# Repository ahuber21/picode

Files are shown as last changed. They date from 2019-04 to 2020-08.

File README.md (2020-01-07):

# picode - All code that is run on the Saufhaengerle Raspberry Pi

* [picode - All code that is run on the Saufhaengerle Raspberry Pi](#picode---all-code-that-is-run-on-the-saufhaengerle-raspberry-pi)
  * [Links](#links)
  * [TODO](#todo)
  * [Contents](#contents)
    * [switcher](#switcher)
    * [zapfhahn](#zapfhahn)
  * [Timezone notes](#timezone-notes)
  * [Install pyfingerprint](#install-pyfingerprint)
    * [pyfingerprint - required modifications / hacks](#pyfingerprint---required-modifications--hacks)
  * [Fixing the image download from charBuffer](#fixing-the-image-download-from-charbuffer)
    * [Using fingerprint sensor](#using-fingerprint-sensor)
  * [Valve notes](#valve-notes)
  * [MariaDB notes](#mariadb-notes)
    * [phpMyAdmin](#phpmyadmin)
    * [Grafana](#grafana)

## Links

* saufanlage myPhpAdmin: http://saufanlage.local:81/http://saufanlage.local:81/phpmyadmin/
  * suffi - NU-AD-76
* saufanlage grafana: http://saufanlage.local:3000
  * admin - NU-AD-76

## TODO

* Multiple fingers per user
  * Fingerprint class?
* Only valves that are registered for user
* Auto-close when idle, i.e. no quantity for x seconds
* Logs to website
* Web terminal
* Android app with push notifications
  * some statistics for every tap
* Web interface for valve/daemon configuration
* Web interface to start calib?
* Warning when tapped quantity threshold is reached
* 4 digit display

Code here is set up for python version 3.X and all required packages are defined in `requirements.txt`.

To set up the RPi do

```bash
# first make sure you installed python3.X + some dev libs
sudo apt-get install python3 python3-dev libtiff5-dev zlib1g-dev libfreetype6-dev liblcms2-dev libwebp-dev libharfbuzz-dev libfribidi-dev tcl8.6-dev tk8.6-dev python-tk git python3-venv emacs devscripts equivs libjpeg-dev apt-get install python3-dev
```

(most of the requirements are for `Pillow` which is required by pyfingerprint)

Now set up the virtual environment

```bash
git clone --recursive https://gitlab.com/saufhaengerle/picode
cd picode
python3.7 -m venv venv
source venv/bin/activate
pip install -r requirements.txt
```

If you want to set up the repository for development, **additional steps** are required. After completing the steps above do

```bash
pre-commit install
```

## Contents

### switcher

A webapp that can switch attached relays. Usually used for switching lights.

Notes:

* Bootstrap version 2.3.2
* Bootstrap toggle from http://www.bootstraptoggle.com/

### zapfhahn

All the code that is required to run the Zapfhahn.

## Timezone notes

Make sure that you select the correct timezone!

```bash
$ sudo raspi-config
# select Europe/Berlin in option '4. Localisation options'
```

## Install pyfingerprint

```bash
# dirty hack because pip install does not actually install the package, only sets the context
mkdir venv/lib/python3.5/site-packages/pyfingerprint
cp src/zapfhahn/hardware/pyfingerprint/src/files/pyfingerprint/pyfingerprint.py venv/lib/python3.5/site-packages/pyfingerprint
```

In order to use the Raspberry Pi's serial port I had to make change that is explained [here](https://raspberrypi.stackexchange.com/questions/45570/how-do-i-make-serial-work-on-the-raspberry-pi3-pi3b-pizerow/45571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). More informatio$

Do

```bash
sudo emacs -nw /boot/config.txt
```

and add the lines

```
enable_uart=1
dtoverlay=pi3-disable-bt
```

Further /boot/cmdline.txt needs some editing to prevent the console from using the UART

```bash
sudo emacs -nw /boot/cmdline.txt
```

and remove the following entry

```
console=serial0,115200
```

It is also necessary to disable the system service that initialises the modem so it doesn't use the UART: `sudo systemctl disable hciuart`.

After rebooting, this will make the uart pins available as `/dev/ttyAMA0` or better `/dev/serial0`.

To install minicom use

```bash
$ sudo apt-get install minicom
```

Now you can test the serial port, shortcut TX and RX on the pi and run the following code

```bash
$ sudo minicom -b 57600 -o -D /dev/serial0
```

If everything is working correctly the terminal will echo every keystroke.

### pyfingerprint - required modifications / hacks

We've tried many libraries and the different notes a bit spread over multiple READMEs.
Now we are using the pyfingerprint library directly in python and the notes about the wiring are in the [FPM-pi README](https://gitlab.com/saufhaengerle/picode/blob/master/src/zapfhahn/hardware/FPM-pi/README.md)

There is a special feature about the R551 sensor that needs a slight modification in the pyfingerprint library.
It is discussed in [this thread](https://github.com/brianrho/FPM/issues/8) and the fix for python is inspired by [these lines](if (page == 0 && group_idx == 0 && fid == 0)).

The point is that when scanning the page IDs for some reason the first bit in the first pageElement is always `False`.
This makes the library think that ID#0 is free, always.
For that reason the first entry must be skipped.
Specifically, this means replacing these lines

```python
# in pyfingerprint.py - function is getTemplateIndex(self, page)
for pageElement in pageElements:
    ## Test every bit (bit = template position is used indicator) of a table page element
    for p in range(0, 7 + 1):
        positionIsUsed = (self.__bitAtPosition(pageElement, p) == 1)
        templateIndex.append(positionIsUsed)
```

with

```python
for idx, pageElement in enumerate(pageElements):
    ## Test every bit (bit = template position is used indicator) of a table page element
    for p in range(0, 7 + 1):
        if idx == 0 and p == 0: continue
        positionIsUsed = (self.__bitAtPosition(pageElement, p) == 1)
        templateIndex.append(positionIsUsed)
```

## Fixing the image download from charBuffer

In the `loadTemplate` method something goes wrong.
We have to replace

```python
        packetPayload = (
            FINGERPRINT_LOADTEMPLATE,
            charBufferNumber,
            self.__rightShift(positionNumber, 8),
            self.__rightShift(positionNumber, 0),
        )
```

with

```python
        packetPayload = (
            FINGERPRINT_LOADTEMPLATE,
            charBufferNumber,
            self.__rightShift(positionNumber, 8),
            self.__rightShift(positionNumber, 0) & 0xFF,
        )
```

i.e., we have to add the `& 0xFF` part.

### Using fingerprint sensor

We use the [WiringPi](http://wiringpi.com/download-and-install/) library to provide the external functions.

**WiringPi is pre-installed on raspian!**

This code was developed using

```bash
pi@octopi:~/saufhaengerle/picode/src/zapfhahn/hardware/FPM-C $ gpio -v
gpio version: 2.46
Copyright (c) 2012-2018 Gordon Henderson
This is free software with ABSOLUTELY NO WARRANTY.
For details type: gpio -warranty

Raspberry Pi Details:
  Type: Pi 3, Revision: 02, Memory: 1024MB, Maker: Sony
  * Device tree is enabled.
  *--> Raspberry Pi 3 Model B Rev 1.2
  * This Raspberry Pi supports user-level GPIO access.
```

In order to use the Raspberry Pi's serial port I had to make change that is explained [here](https://raspberrypi.stackexchange.com/questions/45570/how-do-i-make-serial-work-on-the-raspberry-pi3-pi3b-pizerow/45571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). More information can also be found [here](https://www.raspberrypi.org/documentation/configuration/uart.md)

Do

```bash
sudo emacs -nw /boot/config.txt
```

and add the lines

```
enable_uart=1
dtoverlay=pi3-disable-bt
```

Further /boot/cmdline.txt needs some editing to prevent the console from using the UART

```bash
sudo emacs -nw /boot/cmdline.txt
```

and remove the following entry

```
console=serial0,115200
```

It is also necessary to disable the system service that initialises the modem so it doesn't use the UART: `sudo systemctl disable hciuart`.

After rebooting, this will make the uart pins available as `/dev/ttyAMA0` or better `/dev/serial0`.

The code can be compiled using

 ```bash
 gcc -lwiringPi -o test fpm_raspi.c
 ```

 #### Wiring

The picture shows how the sensor was connected to the RPi.

Wiring to RasPi

It is installed according to the manual, with pins 1 and 7 left disconnected.
Only the UART, 3.3V and GND pins are connected.

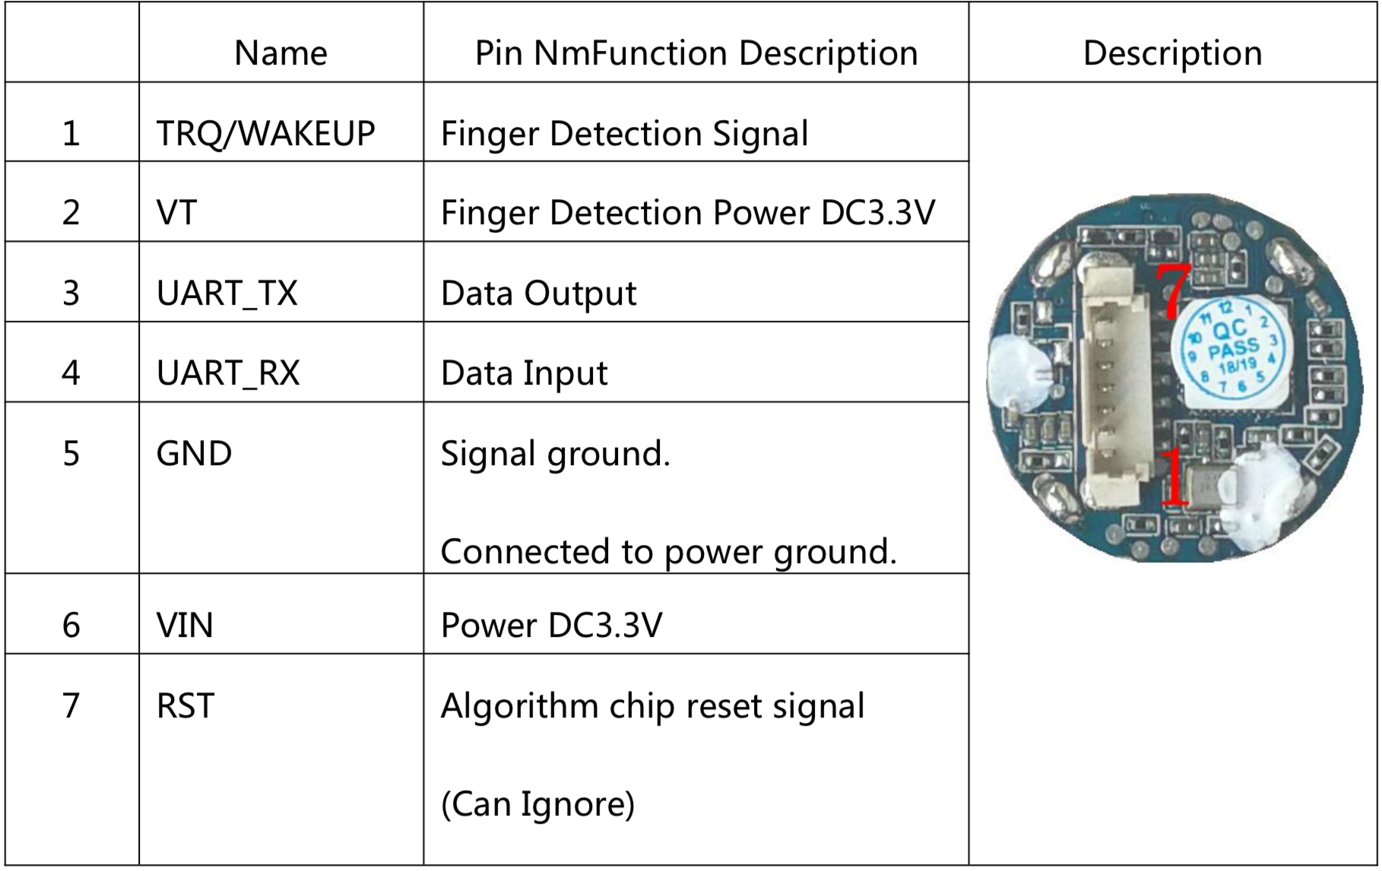
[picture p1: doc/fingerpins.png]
Fingerprint sensor pinout


The pins on the RPi 3 Model B are labeled like this

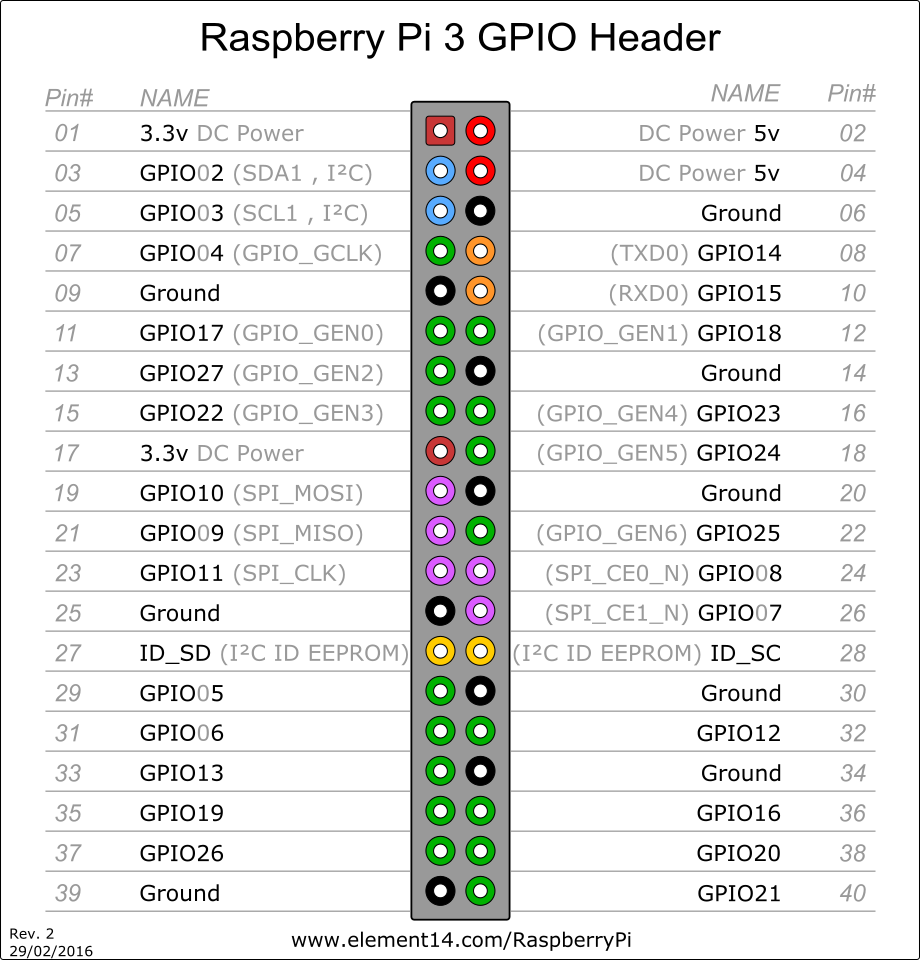
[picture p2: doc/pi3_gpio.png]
Pi Pins


The pins on the Raspberry Pi Zero are labeled like this

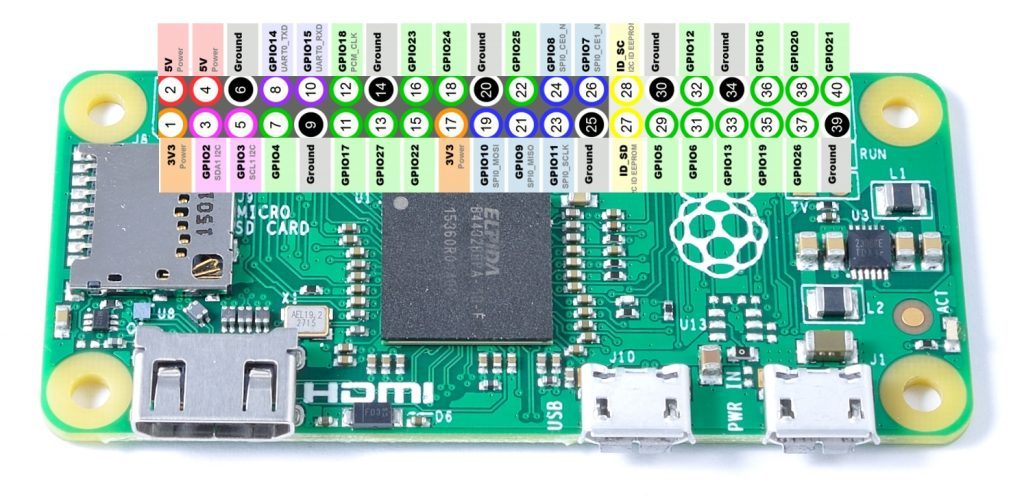
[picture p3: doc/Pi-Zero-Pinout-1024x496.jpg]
Pi Zero Pins


We have these connections

| Sensor pin | Sensor cable color | RPi pin | RPi color | Comment |
|---|---|---|---|---|
| 1 | orange | not connected | | |
| 2 | white | 3.3V/01 | black | |
| 3 | blue | GPIO15 TX/10  | orange/purple | RPi TX->Sensor RX |
| 4 | green | GPIO14 RX/08  | yellow/blue | RPi RX->Sensor TX |
| 5 | yellow | GND | green | |
| 6 | black | 3.3V/17 | yellow | |
| 7 | red | not connected | | |

## Valve notes

The valves run on 12V DC power.
The polarity does not matter.
We connect them to a relay that controls their state.
In my test setup I connected them to the normally open (NO) port.
That is because the data pin is usually in HIGH mode and we have to explicitly pull it down.
Like this, the current draw is 0 until we open it with `valve.open()`.
The logic side of the 5V relay was connected GND, Vcc = 5V and the data pin was connected to the raspberry pi **using a logic level converter**.

## MariaDB notes

```bash
sudo apt-get install mariadb-server
```

Then run the setup script

```bash
$ sudo mysql_secure_installation

NOTE: RUNNING ALL PARTS OF THIS SCRIPT IS RECOMMENDED FOR ALL MariaDB
      SERVERS IN PRODUCTION USE!  PLEASE READ EACH STEP CAREFULLY!

In order to log into MariaDB to secure it, we'll need the current
password for the root user.  If you've just installed MariaDB, and
you haven't set the root password yet, the password will be blank,
so you should just press enter here.

Enter current password for root (enter for none):
OK, successfully used password, moving on...

Setting the root password ensures that nobody can log into the MariaDB
root user without the proper authorisation.

You already have a root password set, so you can safely answer 'n'.

Change the root password? [Y/n] n
 ... skipping.

By default, a MariaDB installation has an anonymous user, allowing anyone
to log into MariaDB without having to have a user account created for
them.  This is intended only for testing, and to make the installation
go a bit smoother.  You should remove them before moving into a
production environment.

Remove anonymous users? [Y/n] n
 ... skipping.

Normally, root should only be allowed to connect from 'localhost'.  This
ensures that someone cannot guess at the root password from the network.

Disallow root login remotely? [Y/n] Y
 ... Success!

By default, MariaDB comes with a database named 'test' that anyone can
access.  This is also intended only for testing, and should be removed
before moving into a production environment.

Remove test database and access to it? [Y/n] Y
 - Dropping test database...
 ... Success!
 - Removing privileges on test database...
 ... Success!

Reloading the privilege tables will ensure that all changes made so far
will take effect immediately.

Reload privilege tables now? [Y/n] Y
 ... Success!

Cleaning up...

All done!  If you've completed all of the above steps, your MariaDB
installation should now be secure.

Thanks for using MariaDB!
```

Create a user with privileges that is allowed to connect from subnet

```
$ sudo mysql -u root
Welcome to the MariaDB monitor.  Commands end with ; or \g.
Your MariaDB connection id is 9
Server version: 10.1.38-MariaDB-0+deb9u1 Raspbian 9.0

Copyright (c) 2000, 2018, Oracle, MariaDB Corporation Ab and others.

Type 'help;' or '\h' for help. Type '\c' to clear the current input statement.

MariaDB [(none)]> GRANT ALL PRIVILEGES ON *.* TO 'suffi'@'localhost' IDENTIFIED BY 'NU-AD-76';
Query OK, 0 rows affected (0.00 sec)
```

We also add a read-only user for grafana

```bash
GRANT SELECT,SHOW VIEW ON *.* TO 'grafana'@'localhost' IDENTIFIED BY 'grafana_view_user';
```

#### Backing up the DB

Export it using

```bash
$ mysqldump -u suffi -p SaufDatabase > SaufDatabase.sql.bak
```

Import it with

```bash
# only necessary if the DB doesn't already exist
$ mysql -u suffi -p
CREATE DATABASE SaufDatabase;
```

and

```bash
mysql -u suffi -p SaufDatabase < SaufDatabase.sql.bak
```

### phpMyAdmin

```bash
sudo apt-get install phpmyadmin
# note: select apache2 if asked
# select yes when asked if you want to generate a DB
# provide password (recommended NU-AD-76)
```

Add phpmyadmin apache conf

```bash
$ sudo emacs -nw /etc/apache2/apache2.conf
# at bottom insert
Include /etc/phpmyadmin/apache.conf
# restart apache
$ sudo /etc/init.d/apache2 restart
```

If you want to make the server listen to a different port edit

```bash
$ sudo emacs -nw /etc/apache2/apache2.conf
$ sudo /etc/init.d/apache2 restart
```

Link the phpMyAdmin landing page

```bash
sudo ln -s /usr/share/phpmyadmin /var/www/html
```

Now you can connect to it, e.g. on `http://192.168.178.86:81/phpmyadmin`

### Grafana

```bash
$ wget https://dl.grafana.com/oss/release/grafana-rpi_6.2.1_armhf.deb
$ sudo dpkg -i grafana-rpi_6.2.1_armhf.deb
```

Add grafana to autostart

```bash
$ sudo /bin/systemctl daemon-reload
$ sudo /bin/systemctl enable grafana-server
```

The grafana server is listening on port 3000.
Log in on `http://192.168.178.86:3000` using user admin with password admin.
Grafana will ask you to change the PW after your first login.
Of course we change it to NU-AD-76.

There we can add a database

* Type: MySQL
* Host: localhost:3306
* Database: SaufDatabase
* User: grafana
* Password: grafana_view_user

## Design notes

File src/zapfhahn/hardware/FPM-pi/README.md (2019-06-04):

* [ahoenle:](#ahoenle)
* [Generic C library for R3xx/ZFMxx/FPMxx/R551 fingerprint modules](#generic-c-library-for-r3xxzfmxxfpmxxr551-fingerprint-modules)

## ahoenle:

Original README below, this was added by ahoenle on 2019-04-19.

_Here begins the original README:_

## Generic C library for R3xx/ZFMxx/FPMxx/R551 fingerprint modules

To use it, the following interface needs to be provided to the library, which expects function pointers with these prototypes:

    /* to get the millisecond count since reset */
    uint32_t (*fpm_millis_func)(void);

    /* millisecond delays */
    void (*fpm_delay_func)(uint32_t interval);

    /* to read from the UART port connected to the module */
    uint16_t (*fpm_uart_read_func)(uint8_t * bytes, uint16_t len);

    /* to write to the UART port connected to the module */
    void (*fpm_uart_write_func)(uint8_t * bytes, uint16_t len);

    /* to get the current number of available bytes to be read */
    uint16_t (*fpm_uart_avail_func)(void);

Check out the examples for details.

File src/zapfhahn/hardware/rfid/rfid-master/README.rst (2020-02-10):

MFRC522
=======







Arduino library for MFRC522 and other RFID RC522 based modules.

Read and write different types of Radio-Frequency IDentification (RFID) cards
on your Arduino using a RC522 based reader connected via the Serial Peripheral
Interface (SPI) interface.

.. _development:
Development
----------

**The development by owner miguelbalboa has ended**.

**Feature status: complete freeze**; no function or API change

**Code status: paritial freeze**; just fixes/typos or documentation updates; *no* extentions for other boards; *no* new examples

**Maintenance status: sporadically**

**Why no further development?**
This library has a long history and is used in many projects. This projects often do not document what version they use. Commiting changes maybe brake those old project and lead to bad experience (for beginners) and support request. For those reasons the library is in freeze mode. You can still commit typo, documentation or bug fixes.

.. _before buy:
Before buy
----------
Please notice that there are many sellers (ebay, aliexpress, ..) who sell mfrc522 boards. **The quality of these boards are extremely different.** Some are soldered with wrong/low quality capacitors or fake/defect mfrc522.

**Please consider buying several devices from different suppliers.** So the chance of getting a working device is higher.

If you got a bad board and you can tell us how to detect those boards (silk, chip description, ..), please share your knowledge.

.. _what works and not:
What works and not?
----------

* **Works**

  #. Communication (Crypto1) with MIFARE Classic (1k, 4k, Mini).
  #. Communication (Crypto1) with MIFARE Classic compatible PICCs.
  #. Firmware self check of MFRC522.
  #. Set the UID, write to sector 0, and unbrick Chinese UID changeable MIFARE cards.
  #. Manage the SPI chip select pin (aka SS, SDA)

* **Works partially**

  #. Communication with MIFARE Ultralight.
  #. Other PICCs (Ntag216).
  #. More than 2 modules, require a multiplexer `#191 <https://github.com/miguelbalboa/rfid/issues/191#issuecomment-242631153>`_.

* **Doesn't work**

  #. MIFARE DESFire, MIFARE DESFire EV1/EV2, not supported by software.
  #. Communication with 3DES or AES, not supported by software.
  #. Peer-to-peer (ISO/IEC 18092), not `supported by hardware`_.
  #. Communication with smart phone, not `supported by hardware`_.
  #. Card emulation, not `supported by hardware`_.
  #. Use of IRQ pin. But there is a proof-of-concept example.
  #. With Arduino Yun see `#111 <https://github.com/miguelbalboa/rfid/issues/111>`_, not supported by software.
  #. With Intel Galileo (Gen2) see `#310 <https://github.com/miguelbalboa/rfid/issues/310>`__, not supported by software.
  #. Power reduction modes `#269 <https://github.com/miguelbalboa/rfid/issues/269>`_, not supported by software.
  #. I2C instead of SPI `#240 <https://github.com/miguelbalboa/rfid/issues/240>`_, not supported by software.
  #. UART instead of SPI `#281 <https://github.com/miguelbalboa/rfid/issues/281>`_, not supported by software.

* **Need more?**

  #. If software: code it and make a pull request.
  #. If hardware: buy a more expensive like PN532 (supports NFC and many more, but costs about $15 and not usable with this library).

.. _compatible ide:
Compatible IDE
----------
This library works with Arduino IDE 1.6, older versions are **not supported** and will cause compiler errors. The built-in library manager is supported.

If you use your own compiler, you have to enable ``c++11``-support.

.. _compatible boards:
Compatible boards
----------

**!!!Only for advanced users!!!**

This library is compatible with the Teensy and ESP8266 if you use the board plugin of the Arduino IDE. Not all examples are available for every board. You also have to change pins. See `pin layout`_.

Some user made some patches/suggestions/ports for other boards:

* Linux: https://github.com/miguelbalboa/rfid/pull/216
* chipKIT: https://github.com/miguelbalboa/rfid/pull/230
* ESP8266 (native): https://github.com/miguelbalboa/rfid/pull/235
* LPCOPen (in C): https://github.com/miguelbalboa/rfid/pull/258

Note that the main target/support of library is still Arduino.

.. _support issue:
Support/issue
----------
1. First checkout `what works and not`_ and `troubleshooting`_ .

2. It seems to be a hardware issue or you need support to program your project?
    Please ask in the official `Arduino forum`_, where you would get a much faster answer than on Github.

3. It seems to be a software issue?
    Open an issue on Github.

.. _code style:
Code style
----------

Please use ``fixed integers``, see `stdint.h`_. Why? This library is compatible with different boards which use different architectures (16bit and 32bit.) Unfixed ``int`` variables have different sizes in different environments and may cause unpredictable behaviour.

.. _pin layout:
Pin Layout
----------

The following table shows the typical pin layout used:

+-----------+----------+---------------------------------------------------------------+--------------------------+
|           | PCD      | Arduino                                                       | Teensy                   |
|           +----------+-------------+---------+---------+-----------------+-----------+--------+--------+--------+
|           | MFRC522  | Uno / 101   | Mega    | Nano v3 |Leonardo / Micro | Pro Micro | 2.0    | ++ 2.0 | 3.1    |
+-----------+----------+-------------+---------+---------+-----------------+-----------+--------+--------+--------+
| Signal    | Pin      | Pin         | Pin     | Pin     | Pin             | Pin       | Pin    | Pin    | Pin    |
+===========+==========+=============+=========+=========+=================+===========+========+========+========+
| RST/Reset | RST      | 9 [1]_      | 5 [1]_  | D9      | RESET / ICSP-5  | RST       | 7      | 4      | 9      |
+-----------+----------+-------------+---------+---------+-----------------+-----------+--------+--------+--------+
| SPI SS    | SDA [3]_ | 10 [2]_     | 53 [2]_ | D10     | 10              | 10        | 0      | 20     | 10     |
+-----------+----------+-------------+---------+---------+-----------------+-----------+--------+--------+--------+
| SPI MOSI  | MOSI     | 11 / ICSP-4 | 51      | D11     | ICSP-4          | 16        | 2      | 22     | 11     |
+-----------+----------+-------------+---------+---------+-----------------+-----------+--------+--------+--------+
| SPI MISO  | MISO     | 12 / ICSP-1 | 50      | D12     | ICSP-1          | 14        | 3      | 23     | 12     |
+-----------+----------+-------------+---------+---------+-----------------+-----------+--------+--------+--------+
| SPI SCK   | SCK      | 13 / ICSP-3 | 52      | D13     | ICSP-3          | 15        | 1      | 21     | 13     |
+-----------+----------+-------------+---------+---------+-----------------+-----------+--------+--------+--------+

+-----------+---------------+
|           | ESP8266       |
|           +---------------+
|           | Wemos D1 mini |
+-----------+---------------+
| Signal    | Pin           |
+===========+===============+
| RST/Reset | D3            |
+-----------+---------------+
| SPI SS    | D8            |
+-----------+---------------+
| SPI MOSI  | D7            |
+-----------+---------------+
| SPI MISO  | D6            |
+-----------+---------------+
| SPI SCK   | D5            |
+-----------+---------------+

.. [1] Configurable, typically defined as RST_PIN in sketch/program.
.. [2] Configurable, typically defined as SS_PIN in sketch/program.
.. [3] The SDA pin might be labeled SS on some/older MFRC522 boards.

.. _hardware:
Hardware
--------

There are three hardware components involved:

1. **Micro Controller**:

* An `Arduino`_ or compatible executing the Sketch using this library.

* Prices vary from USD 7 for clones, to USD 75 for "starter kits" (which
  might be a good choice if this is your first exposure to Arduino;
  check if such kit already includes the Arduino, Reader, and some Tags).

2. **Proximity Coupling Device (PCD)**:

* The PCD is the actual RFID **Reader** based on the `NXP MFRC522`_ Contactless
  Reader Integrated Circuit.

* Readers can be found on `eBay`_ for around USD 5: search for *"rc522"*.

* You can also find them on several web stores. They are often included in
  *"starter kits"*, so check your favourite electronics provider as well.

3. **Proximity Integrated Circuit Card (PICC)**:

* The PICC is the RFID **Card** or **Tag** using the `ISO/IEC 14443A`_
  interface, for example Mifare or NTAG203.

* One or two might be included with the Reader or *"starter kit"* already.

.. _protocol:
Protocols
---------

1. The micro controller and the reader use SPI for communication.

* The protocol is described in the `NXP MFRC522`_ datasheet.

* See the `Pin Layout`_ section for details on connecting the pins.

2. The reader and the tags communicate using a 13.56 MHz electromagnetic field.

* The protocol is defined in ISO/IEC 14443-3:2011 Part 3 Type A.

  * Details are found in chapter 6 *"Type A – Initialization and anticollision"*.

  * See http://wg8.de/wg8n1496_17n3613_Ballot_FCD14443-3.pdf for a free version
    of the final draft (which might be outdated in some areas).

  * The reader does not support ISO/IEC 14443-3 Type B.

.. _security:
Security
-------
* The **UID** of a card **can not be used** as an unique identification for security related projects. Some Chinese cards allow to change the UID which means you can easily clone a card. For projects like *access control*, *door opener* or *payment systems* you **must implement** an **additional security mechanism** like a password or normal key.

* This library only supports crypto1-encrypted communication. Crypto1 has been known as `broken`_ for a few years, so it does NOT offer ANY security, it is virtually unencrypted communication. **Do not use it for any security related applications!**

* This library does not offer 3DES or AES authentication used by cards like the Mifare DESFire, it may be possible to be implemented because the datasheet says there is support. We hope for pull requests :).

.. _troubleshooting:
Troubleshooting
-------

* **I don't get input from reader** or **WARNING: Communication failure, is the MFRC522 properly connected?**

  #. Check your physical connection, see `Pin Layout`_ .
  #. Check your pin settings/variables in the code, see `Pin Layout`_ .
  #. Check your pin header soldering. Maybe you have cold solder joints.
  #. Check voltage. Most breakouts work with 3.3V.
  #. SPI only works with 3.3V, most breakouts seem 5V tollerant, but try a level shifter.
  #. SPI does not like long connections. Try shorter connections.
  #. SPI does not like prototyping boards. Try soldered connections.
  #. According to reports #101, #126 and #131, there may be a problem with the soldering on the MFRC522 breakout. You could fix this on your own.

* **Firmware Version: 0x12 = (unknown) or other random values**

  #. The exact reason of this behaviour is unknown.
  #. Some boards need more time after `PCD_Init()` to be ready. As workaround add a `delay(4)` directly after `PCD_Init()` to give the PCD more time.
  #. If this sometimes appears, a bad connection or power source is the reason.
  #. If the firmware version is reported permanent, it is very likely that the hardware is a fake or has a defect. Contact your supplier.

* **Sometimes I get timeouts** or **sometimes tag/card does not work.**

  #. Try the other side of the antenna.
  #. Try to decrease the distance between the MFRC522 and your tag.
  #. Increase the antenna gain per firmware: ``mfrc522.PCD_SetAntennaGain(mfrc522.RxGain_max);``
  #. Use better power supply.
  #. Hardware may be corrupted, most products are from china and sometimes the quality is really poor. Contact your seller.

* **My tag/card doesn't work.**

  #. Distance between antenna and token too large (>1cm).
  #. You got the wrong type PICC. Is it really 13.56 MHz? Is it really a Mifare Type A?
  #. NFC tokens are not supported. Some may work.
  #. Animal RFID tags are not supported. They use a different frequency (125 kHz).
  #. Hardware may be corrupted, most products are from china and sometimes the quality is really poor. Contact your seller.
  #. Newer versions of Mifare cards like DESFire/Ultralight maybe not work according to missing authentication, see `security`_ or different `protocol`_.
  #. Some boards bought from Chinese manufactures do not use the best components and this can affect the detection of different types of tag/card. In some of these boards, the L1 and L2 inductors do not have a high enough current so the signal generated is not enough to get Ultralight C and NTAG203 tags to work, replacing those with same inductance (2.2uH) but higher operating current inductors should make things work smoothly. Also, in some of those boards the  harmonic and matching circuit needs to be tuned, for this replace C4 and C5 with 33pf capacitors and you are all set. (Source: `Mikro Elektronika`_)

* **My mobile phone doesn't recognize the MFRC522** or **my MFRC522 can't read data from other MFRC522**

  #. Card simulation is not supported.
  #. Communication with mobile phones is not supported.
  #. Peer to peer communication is not supported.

* **I can only read the card UID.**

  #. Maybe the `AccessBits` have been accidentally set and now an unknown password is set. This can not be reverted.
  #. Probably the card is encrypted. Especially official cards like public transport, university or library cards. There is *no* way to get access with this library.

* **I need more features.**

  #. If software: code it and make a pull request.
  #. If hardware: buy a more expensive chip like the PN532 (supports NFC and many more, but costs about $15)

.. _license:
License
-------
This is free and unencumbered software released into the public domain.

Anyone is free to copy, modify, publish, use, compile, sell, or
distribute this software, either in source code form or as a compiled
binary, for any purpose, commercial or non-commercial, and by any
means.

In jurisdictions that recognize copyright laws, the author or authors
of this software dedicate any and all copyright interest in the
software to the public domain. We make this dedication for the benefit
of the public at large and to the detriment of our heirs and
successors. We intend this dedication to be an overt act of
relinquishment in perpetuity of all present and future rights to this
software under copyright law.

THE SOFTWARE IS PROVIDED "AS IS", WITHOUT WARRANTY OF ANY KIND,
EXPRESS OR IMPLIED, INCLUDING BUT NOT LIMITED TO THE WARRANTIES OF
MERCHANTABILITY, FITNESS FOR A PARTICULAR PURPOSE AND NONINFRINGEMENT.
IN NO EVENT SHALL THE AUTHORS BE LIABLE FOR ANY CLAIM, DAMAGES OR
OTHER LIABILITY, WHETHER IN AN ACTION OF CONTRACT, TORT OR OTHERWISE,
ARISING FROM, OUT OF OR IN CONNECTION WITH THE SOFTWARE OR THE USE OR
OTHER DEALINGS IN THE SOFTWARE.

For more information, please refer to https://unlicense.org/

.. _dependency:
Dependency
----------

* **Arduino.h**

  * From: Arduino IDE / target specific
  * License: (target: Arduino) GNU Lesser General Public License 2.1

* **SPI.h**

  * From: Arduino IDE / target specific
  * License: (target: Arduino) GNU Lesser General Public License 2.1

* **stdint.h**

  * From: Arduino IDE / Compiler and target specific
  * License: different

History
-------

The MFRC522 library was first created in Jan 2012 by Miguel Balboa (from
http://circuitito.com) based on code by Dr. Leong (from http://B2CQSHOP.com)
for *"Arduino RFID module Kit 13.56 Mhz with Tags SPI W and R By COOQRobot"*.

It was translated into English and rewritten/refactored in the fall of 2013
by Søren Thing Andersen (from http://access.thing.dk).

It has been extended with functionality to alter sector 0 on Chinese UID changeable MIFARE card in Oct 2014 by Tom Clement (from http://tomclement.nl).

Maintained by miguelbalboa until 2016.
Maintained by Rotzbua from 2016 until 2018.

.. _arduino: https://arduino.cc/
.. _ebay: https://www.ebay.com/
.. _iso/iec 14443a: https://en.wikipedia.org/wiki/ISO/IEC_14443
.. _iso/iec 14443-3\:2011 part 3:
.. _nxp mfrc522: https://www.nxp.com/documents/data_sheet/MFRC522.pdf
.. _broken: https://eprint.iacr.org/2008/166
.. _supported by hardware: https://web.archive.org/web/20151210045625/http://www.nxp.com/documents/leaflet/939775017564.pdf
.. _Arduino forum: https://forum.arduino.cc
.. _stdint.h: https://en.wikibooks.org/wiki/C_Programming/C_Reference/stdint.h
.. _Mikro Elektronika: https://forum.mikroe.com/viewtopic.php?f=147&t=64203

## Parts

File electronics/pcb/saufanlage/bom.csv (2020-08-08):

Qty | Price/unit | Price total | Name | Manufacturer Part No | Digikey Part No
20 | 0.46 | 9.2 | Capacitor_SMD:C_0805_2012Metric_Pad1.15x1.40mm_HandSolder | C2012X5R0J226M085AB | 445-7678-2-ND
6 | 0.53 | 3.18 | Thermistor | NXFT15WF104FA1B025 | 490-11856-ND
10 | 0.499 | 4.99 | Molex 1x10 2.54 Connector | 22232101 | WM4208-ND
10 | 0.362 | 3.62 | Molex 1x10 2.54 Housing | 22013107 | WM2008-ND
50 | 0.01877 | 0.9385 | ERJ-6RBD1003V | ERJ-6RBD1003V | ERJ-6RBD1003V-ND
 |  | 0
 |  | 0
 |  | 0
 |  | 0
 |  | 0
 |  | 0
 |  | 0
 |  | 0
 |  | 0
 |  | 0
 |  | 0
 |  | 0

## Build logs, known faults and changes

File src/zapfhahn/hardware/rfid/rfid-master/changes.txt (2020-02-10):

-- Add changes to unreleased tag until we make a release.

xx 2019, v1.4.6

12 Jun 2019, v1.4.5
- Library in freeze mode, no new features, no new examples, just bugfixes to keep compability for old projects
- Updated README

31 Mar 2019, v1.4.4
- Fixed example
- Fixed UnbrickUidSector
- Updated comments
- Removed teensy from CI and PlatformIO config

27 Oct 2018, v1.4.3
- Added counterfeit detection and hint about bad boards
- Improved hardware based reset

04 Oct 2018, v1.4.2
- Fixed keywords
- Changed development status of library

04 Oct 2018, v1.4.1
- Replaced UINT8_MAX by UNUSED_PIN
- Replaced default value NULL for pointer with correct nullptr
- Added pin layout for wemos d1 mini @mmone
- Added alternative fritzing layout for mfrc522 reader @jose1711
- Added soft power control functions @Bill2462
- Fixed typo in example ReadAndWrite.ino @Drachenfrucht1
- Fixed grammar @KiddieD
- Fixed infinite loop in example AccessControl.ino @mads256c
- Fixed 0-index key ID equals to 0 fails in AccessControl.ino @thoaitrieu
- Changed type boolean to bool for a more common use @Rotzbua
- Fixed wrong var names in PICC_Select MFRC522.cpp @tuyethoa08041997
- Fixed hang PCD_Init() on non-arduino boards @heziegl
- Fixed possible infinite loop PCD_Reset() @psgreco
- And many thanks to all other contributors

13 Apr 2018, v1.4.0
- Replaced UINT8_MAX by UNUSED_PIN @Rotzbua
- Fixed hang PCD_Init() on non-arduino boards @heziegl
- deprecate MIFARE_SetAccessBits @Rotzbua
- IMPORTANT: v1.4.X will be last version under license "unlicense"

22 Mar 2017, v1.3.6
- Added deprecate and compiler warnings @Rotzbua

8 Apr 2017, v1.3.5
- Updated "AccessControl.ino", bugs fixed and alterate Wipe button polling method without using other library @beyondszine reviewed by @omersiar
- Updated README notice about port for esp8266 @mmmmar

7 Apr 2017, v1.3.4
- Added new example "rfid_read_personal_data.ino" @ryand1011
- Updated example "rfid_write_personal_data.ino" code style to Arduino IDE @Rotzbua
- Removed (temp.) Teensy from travis build script because fails @Rotzbua

26 Mar 2017, v1.3.3
- Fixed bugs in MFRC522Extended, now should work with Desfire.h from JPG-Consulting @Rotzbua
- Fixed UINT8_MAX error @Rotzbua

15 Mar 2017, v1.3.2
- Added ESP8266 to library.properties

15 Mar 2017, v1.3.1
- Fixed compiler warning in MFRC522Extended @Rotzbua
- Removed unused function @Rotzbua

13 Mar 2017, v1.3.0
- Warning: Source has moved to folder src!
- Added addtional class to support ISO/IEC 14443-4 PICCs @JPG-Consulting
- Added RATS (Request for Answer To Select) @JPG-Consulting
- More information see https://github.com/miguelbalboa/rfid/pull/271 @JPG-Consulting

13 Mar 2017, v1.2.1
- Removed need for reset pin #275 @tkoester
- Added SPI speed option + Various minor changes #276 @tuyethoa08041997
- Updated documentation, travis build script and small code change @Rotzbua

3 Jan 2017, v1.2.0
- Warning: This version introduce usage of stdint.h, usage of not well defined int types are abandoned.
           Interface has changed: e.g. long -> int32_t
           @Rotzbua
- Removed problematic example examples/servo_motor/servo_motor.ino @omersiar
- Added examples/AccessControl/AccessControl.ino @omersiar
- Fixed minor issues reported in #211 @omersiar
- Added bad components hint to README @danielcbit
- Fixed selftest @surr
- Fixed auth problem with long UIDs @surr

26 Aug 2016, v1.1.9
- Warning: Only Arduino IDE version 1.6 is supported, please update your IDE to 1.6 to use this Library.
- Added ESP8266 platform support @Rotzbua
- Changed README.rst content to show more info @Rotzbua
- Minor Changes to examples/ReadUidMultiReader/ReadUidMultiReader.ino example @Rotzbua

11 Feb 2016, v1.1.8
- Added examples/MinimalInterrupt/MinimalInterrupt.ino example, Interrupt example @lmmeng
- Added .gitignore file allows the project to be more easily used as a subproject. @BenWiederhake
- Added Added Teensy 2.0 & Tensy++ 2.0 pinouts to README.rst @jkutianski

16 Jan 2016, v1.1.7
- README.rst Spelling and Grammar Tweak @cuthbertnibbles
- Added examples/servo_motor/servo_motor.ino example, Arduino RFID Access Control with a Servo Motor @techied
- Added examples/RFID-Cloner/RFID-Cloner.ino Copy from rfid cards with standard authentication @stefanblommaert
- Fix compile error at examples/RFID-Cloner/RFID-Cloner.ino, using MFRC522:::PICC_Type, @Rotzbua

06 Jan 2016, v1.1.6
- Fixed compilation error for examples/ReadNUID/ReadNUID.ino example. @Rotzbua

04 Jan 2016, v1.1.5
- Use settings functions on SPI libraries, setSPIConfig was deleted, now the library use SPI.beginTransaction() and SPI.endTransaction() @sophiekovalevsky
- Added examples/ReadNUID/ReadNUID.ino example, showing how to read new NUID from a PICC to serial. @sophiekovalevsky

03 Jan 2016, v1.1.4
- Added Authentication with Ntag 213,215,216 returns the pACK MFRC522::PCD_NTAG216_AUTH @Gargantuanman
- Starting to use versions http://semver.org/
- Continuous Integration @ivankravets
- functions return MFRC522::StatusCode and MFRC522::PICC_Type instead of generic byte @rotzbua
- removed int-values of MFRC522::StatusCode and MFRC522::PICC_Type @rotzbua

05 Dec 2015
- recognize infineon cards correctly @mayatforest
- added multi reader support, see example @lmmeng

10 Nov 2014
- Updated the changelog.
- Added makefile.

24 Oct 2014
- Added PlatformIO-based manifest file.

17 Jul 2014
- Written documentation for the library.
- Added rfid_default_keys example.

11 Jun 2014
- Updated example: ReadAndWrite.

14 Apr 2014
- Updated examples: DumpInfo, MifareClassicValueBlock, and ReadAndWrite.

12 Feb 2014
- Fixed resetPowerDownPin initial state.

29 Jan 2014
- Fixed chipSelectPin initial state.

30 Nov 2013
- Examples put in their own folders.
- Updated the keywords.txt file.

12 Nov 2013
- Updated examples: DumpInfo, MifareClassicValueBlock, and ReadAndWrite.

20 Oct 2013
- All constants, functions and parameters are now commented in English.
- Code refactored, most function names have changed.
- Support ISO-14443-3 anti collission and 4/7/10 byte UIDs (cascade levels).
- Added functions for MIFARE Classic Decrement/Increment/Restore/Transfer
  and MIFARE Ultralight Write.
- New examples written.

19 Oct 2013
- Renamed library from RFID to MFRC522 (RFID seemed to generic).
- Register names changed to comply with datasheet.
- Global defines moved into class.

24 Sep 2013
- Turn off encryption when tag is halted.

27 Jan 2013
- Added README and small TODO list.
- Added example to show Serial on LCD display.

09 Sep 2012
- Initial commit to GitHub.

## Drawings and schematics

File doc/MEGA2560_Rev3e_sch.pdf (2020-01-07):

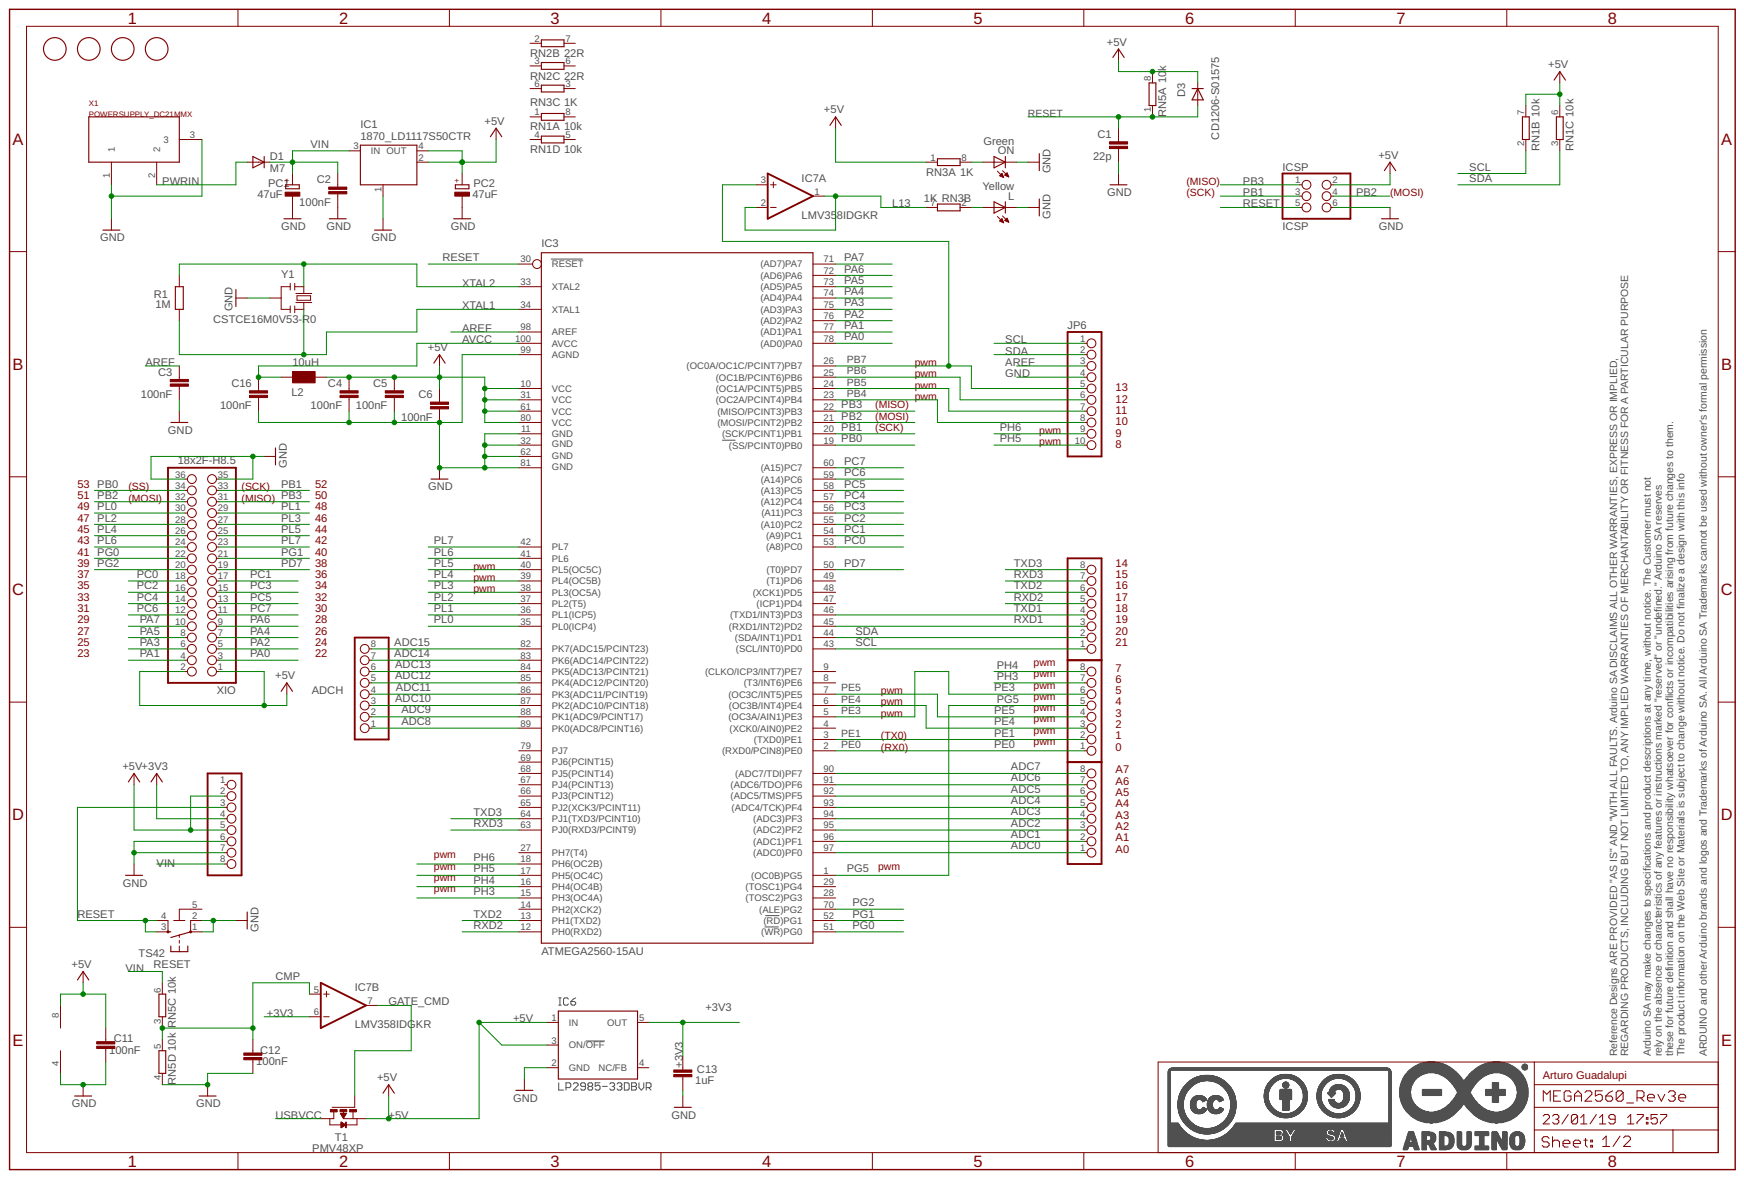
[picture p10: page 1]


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

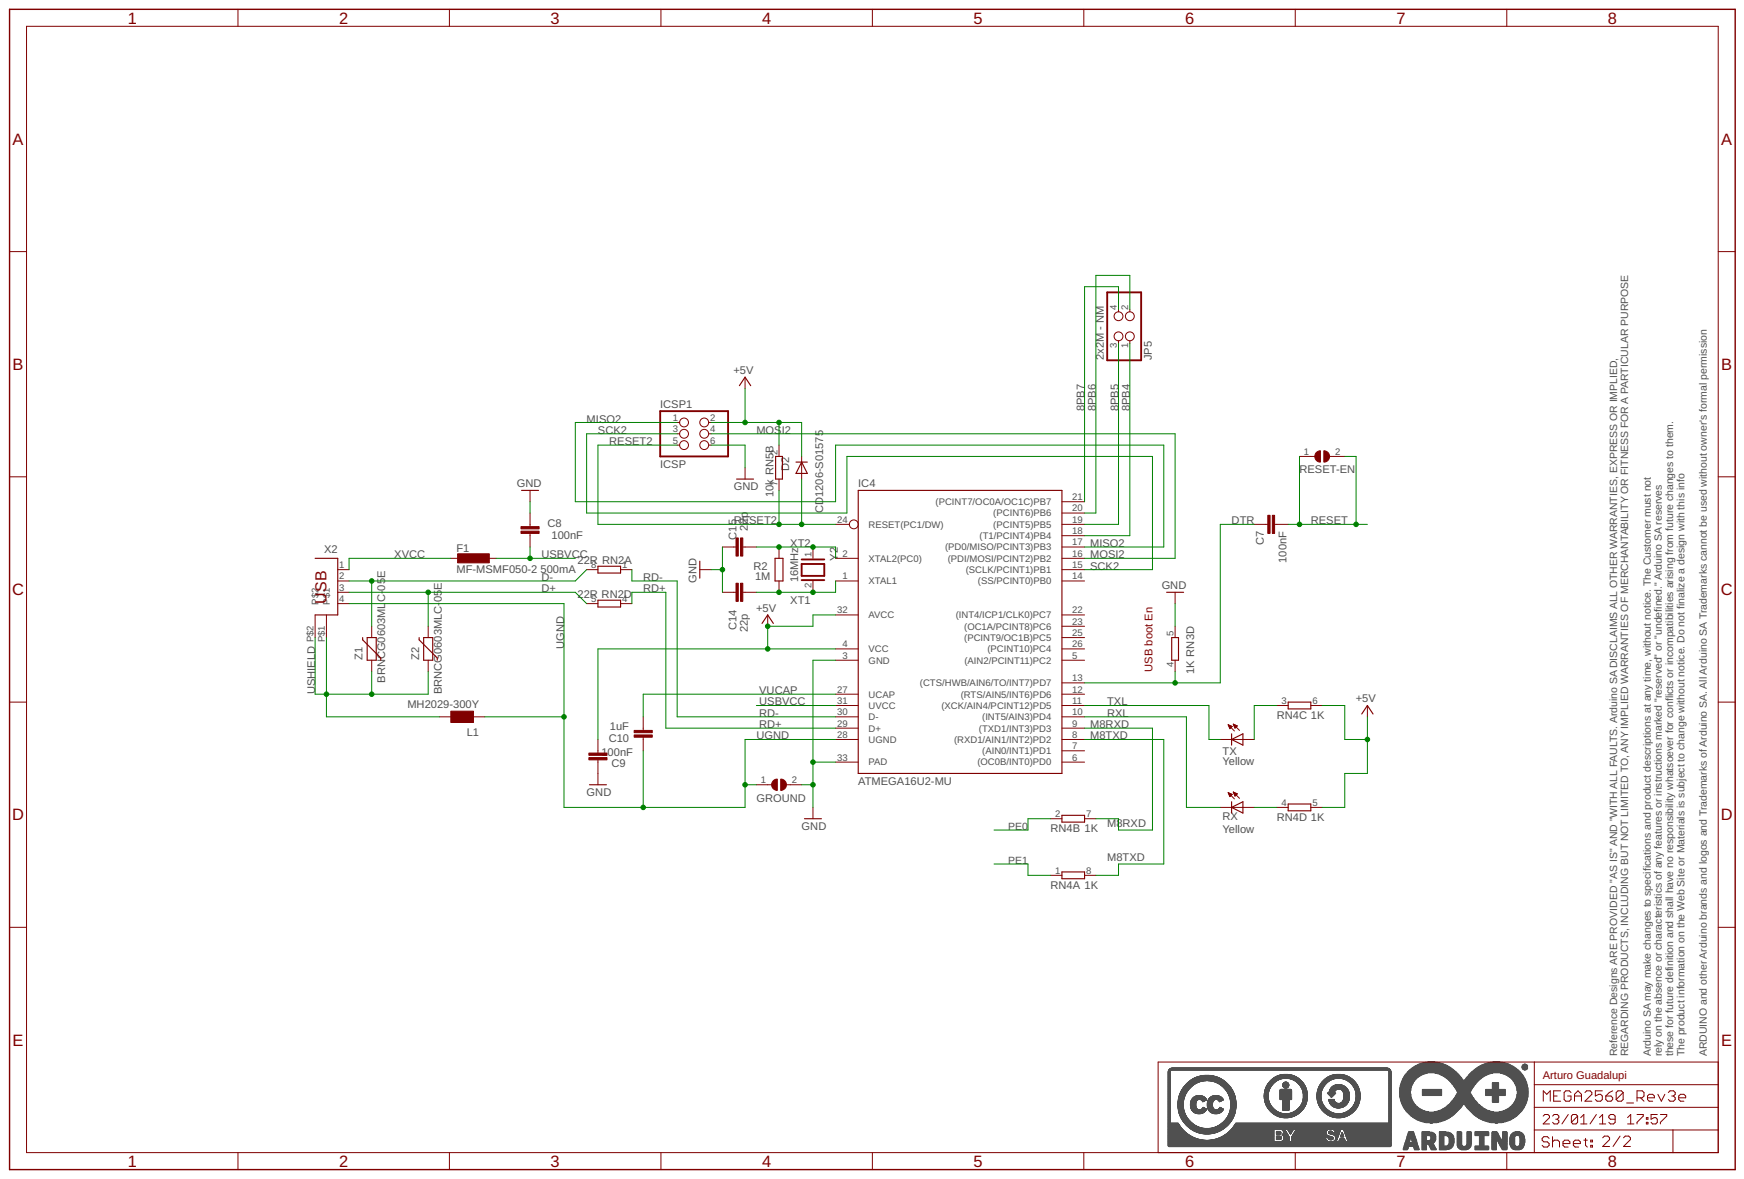
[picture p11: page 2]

Reference Designs ARE PROVIDED "AS IS" AND "WITH ALL FAULTS. Arduino SA DISCLAIMS ALL OTHER WARRANTIES, EXPRESS OR IMPLIED, REGARDING PRODUCTS, INCLUDING BUT NOT LIMITED TO, ANY IMPLIED WARRANTIES OF MERCHANTABILITY OR FITNESS FOR A PARTICULAR PURPOSE Arduino SA may make changes to specifications and product descriptions at any time, without notice. The Customer must not rely on the absence or characteristics of any features or instructions marked "reserved" or "undefined." Arduino SA reserves these for future definition and shall have no responsibility whatsoever for conflicts or incompatibilities arising from future changes to them. The product information on the Web Site or Materials is subject to change without notice. Do not finalize a design with this info ARDUINO and other Arduino brands and logos and Trademarks of Arduino SA. All Arduino SA Trademarks cannot be used without owner's formal permission 100nF GND Yellow Yellow MF-MSMF050-2 500mA +5V 100nF GND 100nF GND 1uF +5V ATMEGA16U2-MU ICSP +5V GND GND MH2029-300Y BRNCG0603MLC-05E BRNCG0603MLC-05E 1K1K 1K1K 10k 1K 22R 22R 1M 16MHz 22p 22p GND 2x2M - NM CD1206-S01575 C8 RXTX 123 P4 $1 P$1 P$2 P$2 X2 F1 C9 C7 1 2 RESET-EN C10 (AIN0/INT1)PD1 7 (AIN2/PCINT11)PC2 5 (CTS/HWB/AIN6/TO/INT7)PD7 13 (INT4/ICP1/CLK0)PC7 22 (INT5/AIN3)PD4 10 (OC0B/INT0)PD0 6 (OC1A/PCINT8)PC6 23 (PCINT5)PB5 19 (PCINT6)PB6 20 (PCINT7/OC0A/OC1C)PB7 21 (PCINT9/OC1B)PC5 25 (PCINT10)PC4 26 (PD0/MISO/PCINT3)PB3 17 (PDI/MOSI/PCINT2)PB2 16 (RTS/AIN5/INT6)PD6 12 (RXD1/AIN1/INT2)PD2 8 (SCLK/PCINT1)PB1 15 (SS/PCINT0)PB0 14 (T1/PCINT4)PB4 18 (TXD1/INT3)PD3 9 (XCK/AIN4/PCINT12)PD5 11 AVCC 32 D+ 29 D- 30 GND 3 PAD 33 RESET(PC1/DW) 24 UCAP 27 UGND 28 UVCC 31 VCC 4 XTAL1 1 XTAL2(PC0) 2 IC4 1 2 3 4 5 6 ICSP1 L1 Z1Z2 1 2 GROUND 1 8 RN4A 2 7 RN4B 3 6 RN4C 4 5 RN4D 2 7 RN5B 4 5 RN3D 8 1 RN2A 5 4 RN2D R2 1 2 Y2 C14 C15 1 2 3 4 JP5 D2 RESET M8RXD M8RXD M8TXD M8TXD PE1 PE0 DTR USBVCC USBVCC VUCAP RD- RD- RD+ RD+ RESET2 RESET2 MISO2 MISO2 MOSI2 MOSI2 SCK2 SCK2 XVCC RXL TXL D- D+ UGND UGND USHIELD XT2 XT1 8PB7 8PB6 8PB5 8PB4 USB boot En Arturo Guadalupi USB ABCDE 1 2 3 4 5 6 7 8 ABCDE 1 2 3 4 5 6 7 8

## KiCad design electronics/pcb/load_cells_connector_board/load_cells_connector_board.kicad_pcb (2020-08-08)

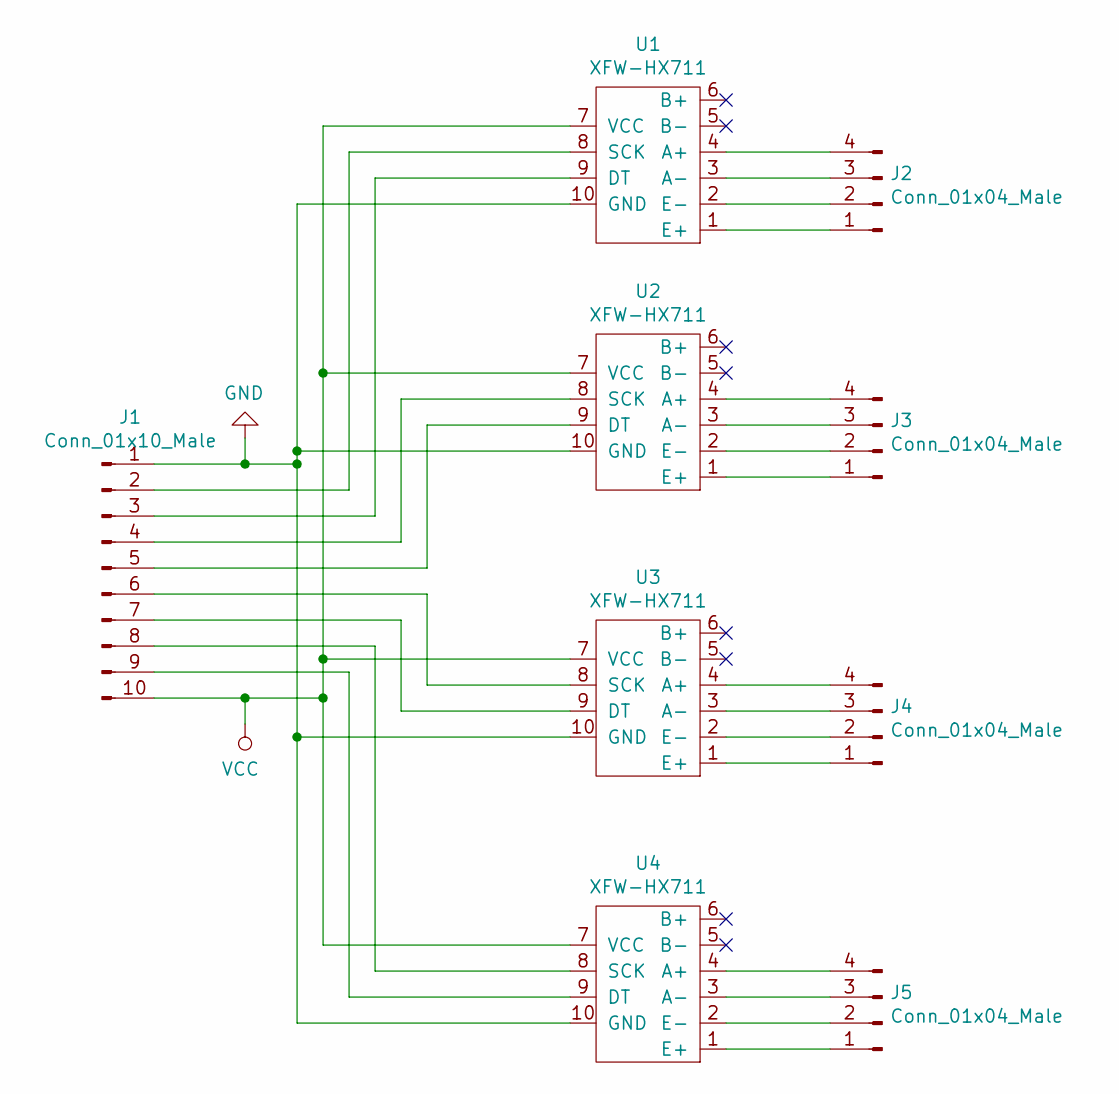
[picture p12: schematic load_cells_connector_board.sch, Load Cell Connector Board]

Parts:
J1: Conn_01x10_Male; Molex_KK-254_AE-6410-10A_1x10_P2.54mm_Vertical
J2, J3, J4, J5: Conn_01x04_Male; Molex_KK-254_AE-6410-04A_1x04_P2.54mm_Vertical
U1, U2, U3, U4: XFW-HX711

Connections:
GND: J1.1, U1.10 (GND), U2.10 (GND), U3.10 (GND), U4.10 (GND)
unnamed: J1.2, U1.8 (SCK)
unnamed: J1.3, U1.9 (DT)
unnamed: J1.4, U2.8 (SCK)
unnamed: J1.5, U2.9 (DT)
unnamed: J1.6, U3.8 (SCK)
unnamed: J1.7, U3.9 (DT)
unnamed: J1.8, U4.8 (SCK)
unnamed: J1.9, U4.9 (DT)
unnamed: J2.1, U1.1 (E+)
unnamed: J2.2, U1.2 (E-)
unnamed: J2.3, U1.3 (A-)
unnamed: J2.4, U1.4 (A+)
unnamed: J3.1, U2.1 (E+)
unnamed: J3.2, U2.2 (E-)
unnamed: J3.3, U2.3 (A-)
unnamed: J3.4, U2.4 (A+)
unnamed: J4.1, U3.1 (E+)
unnamed: J4.2, U3.2 (E-)
unnamed: J4.3, U3.3 (A-)
unnamed: J4.4, U3.4 (A+)
unnamed: J5.1, U4.1 (E+)
unnamed: J5.2, U4.2 (E-)
unnamed: J5.3, U4.3 (A-)
unnamed: J5.4, U4.4 (A+)
VCC: J1.10, U1.7 (VCC), U2.7 (VCC), U3.7 (VCC), U4.7 (VCC)

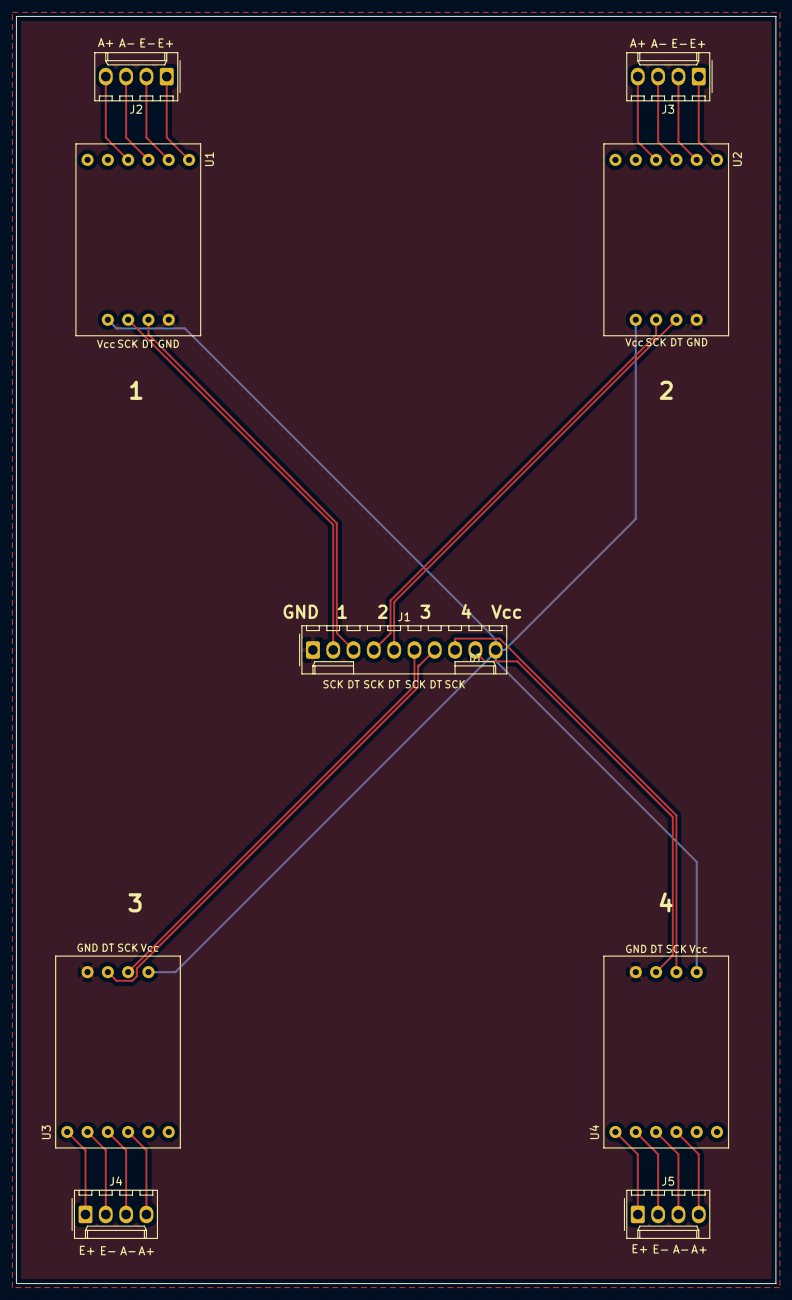
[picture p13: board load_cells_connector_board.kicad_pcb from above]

Board: 2 copper layers, 95.0 x 158.5 mm, 9 parts (0 on the bottom side), 26 nets.

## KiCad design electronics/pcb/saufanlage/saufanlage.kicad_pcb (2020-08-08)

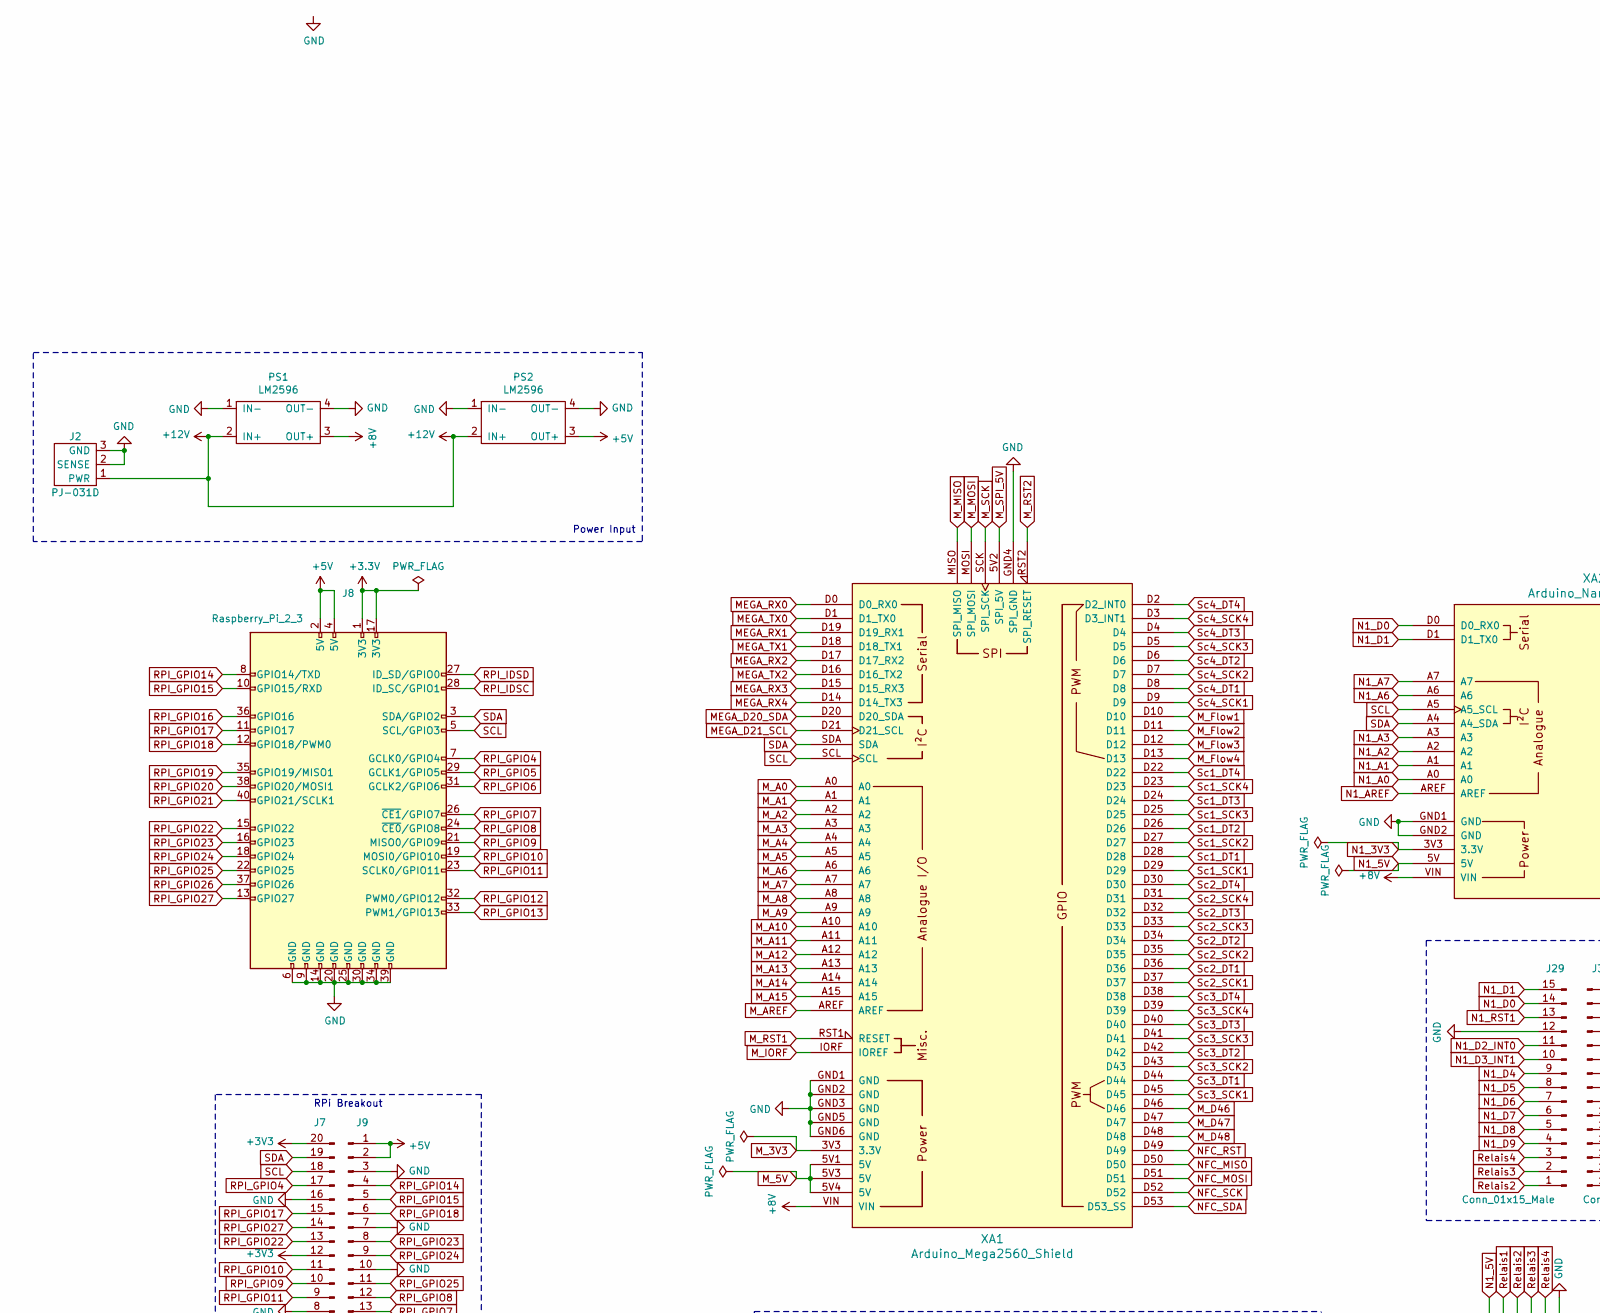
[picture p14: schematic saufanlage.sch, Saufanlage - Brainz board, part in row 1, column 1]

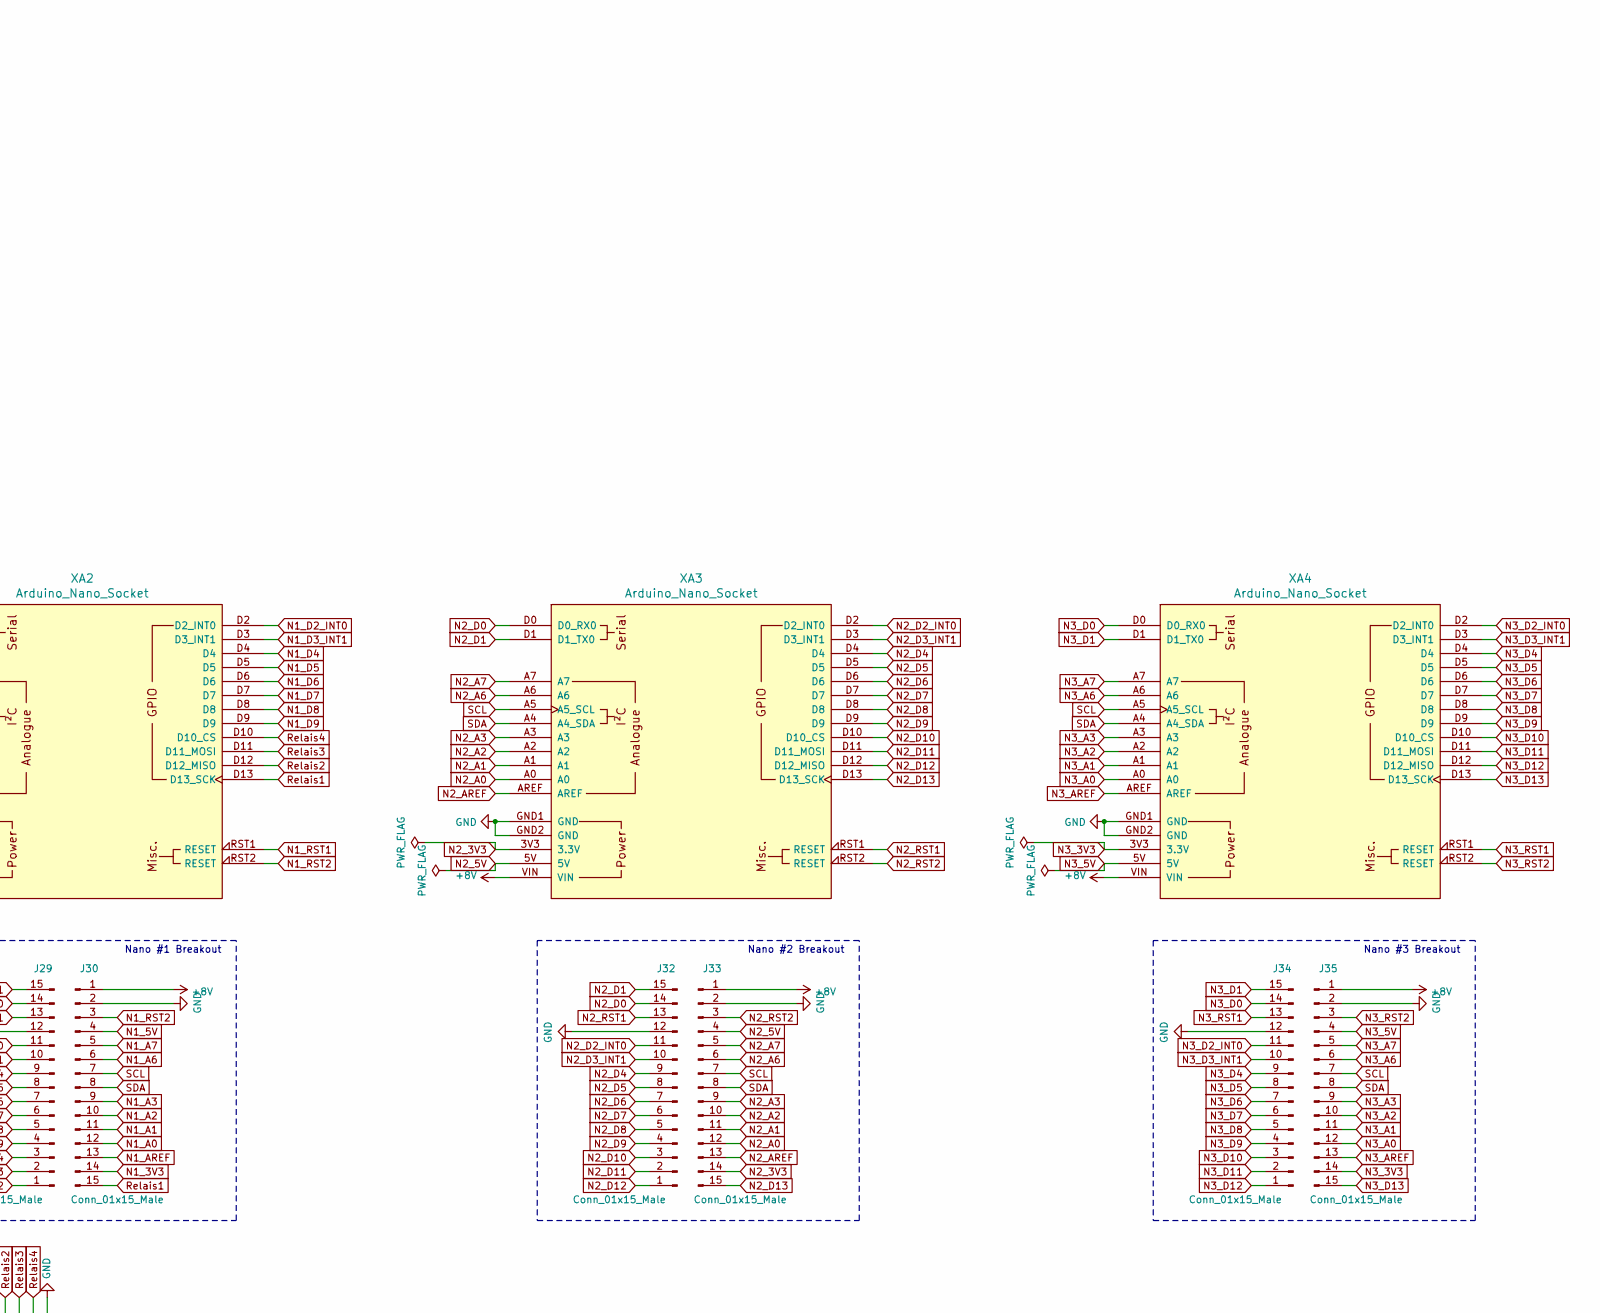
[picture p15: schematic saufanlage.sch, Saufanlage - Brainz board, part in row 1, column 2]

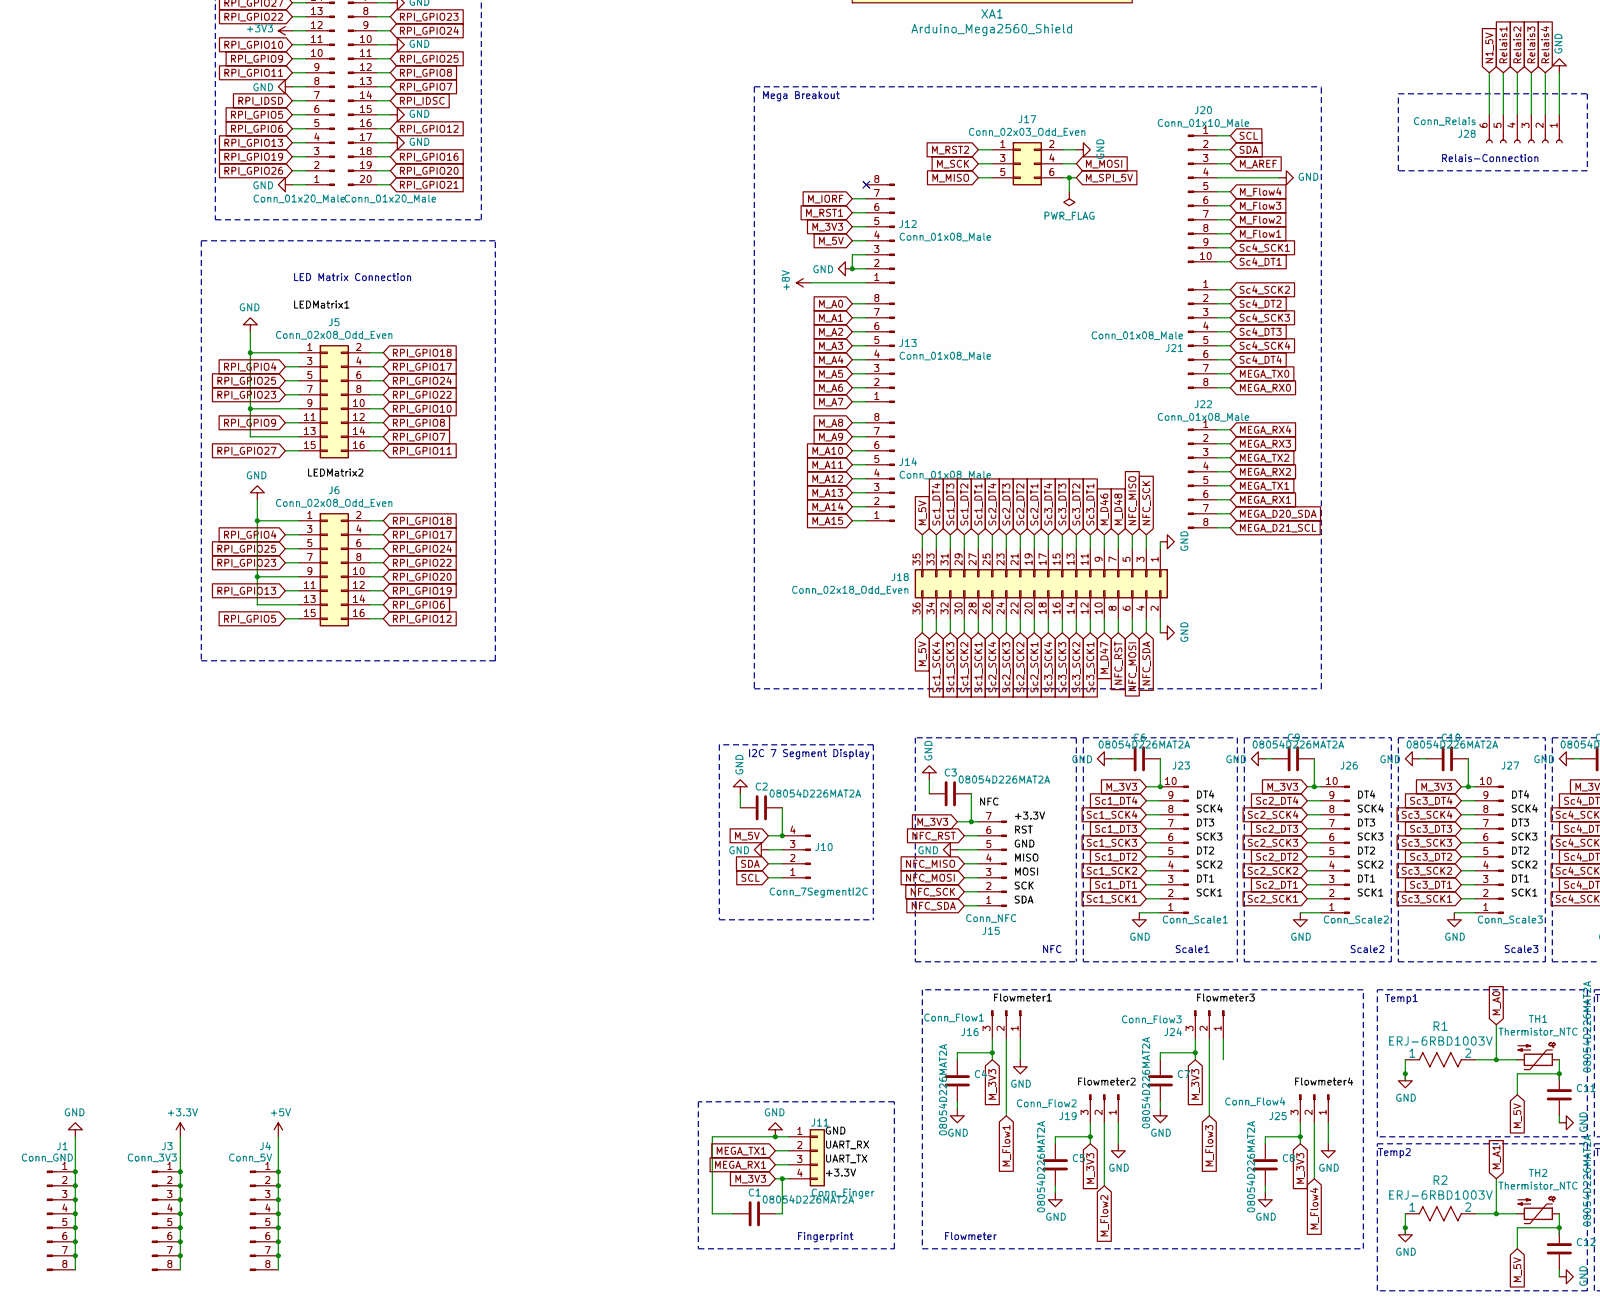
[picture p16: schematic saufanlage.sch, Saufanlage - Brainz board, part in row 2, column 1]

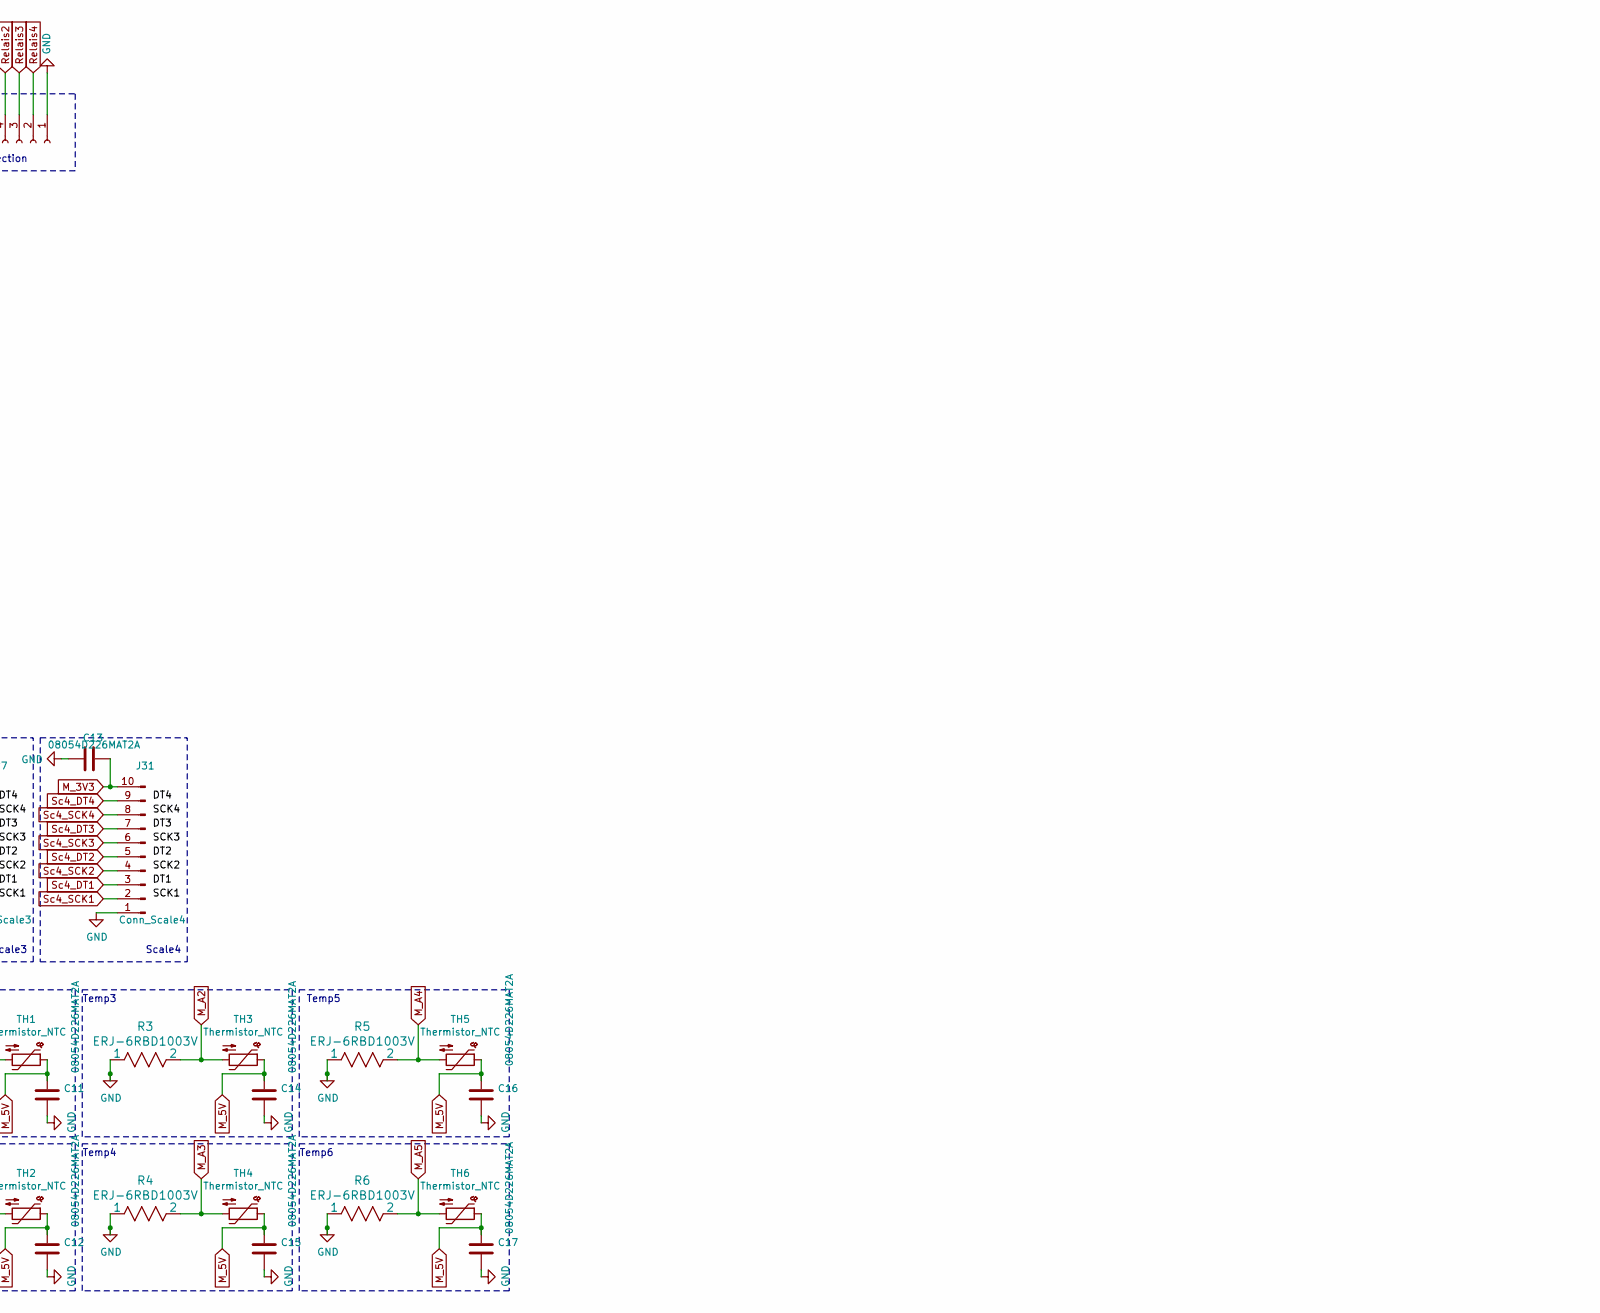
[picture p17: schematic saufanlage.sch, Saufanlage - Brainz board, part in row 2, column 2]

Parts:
C1, C2, C3, C4, C5, C6, C7, C8, C9, C10, C11, C12, C13, C14, C15, C16, C17: 08054D226MAT2A; C_0805_2012Metric_Pad1.15x1.40mm_HandSolder
J1: Conn_GND; PinHeader_1x08_P2.54mm_Vertical
J2: PJ-031D; CUI_PJ-031D
J3: Conn_3V3; PinHeader_1x08_P2.54mm_Vertical
J4: Conn_5V; PinHeader_1x08_P2.54mm_Vertical
J5, J6: Conn_02x08_Odd_Even; PinHeader_2x08_P2.54mm_Vertical
J7, J9: Conn_01x20_Male; PinHeader_1x20_P2.54mm_Vertical
J8: Raspberry_Pi_2_3; PinHeader_2x20_P2.54mm_Vertical
J10: Conn_7SegmentI2C; PinHeader_1x04_P2.54mm_Vertical
J11: Conn_Finger; PinHeader_1x04_P2.54mm_Vertical
J12, J13, J14, J21, J22: Conn_01x08_Male; PinHeader_1x08_P2.54mm_Vertical
J15: Conn_NFC; PinHeader_1x07_P2.54mm_Vertical
J16: Conn_Flow1; PinHeader_1x03_P2.54mm_Vertical
J17: Conn_02x03_Odd_Even; PinHeader_2x03_P2.54mm_Vertical
J18: Conn_02x18_Odd_Even; PinHeader_2x18_P2.54mm_Vertical
J19: Conn_Flow2; PinHeader_1x03_P2.54mm_Vertical
J20: Conn_01x10_Male; PinHeader_1x10_P2.54mm_Vertical
J23: Conn_Scale1; PinHeader_1x10_P2.54mm_Vertical
J24: Conn_Flow3; PinHeader_1x03_P2.54mm_Vertical
J25: Conn_Flow4; PinHeader_1x03_P2.54mm_Vertical
J26: Conn_Scale2; PinHeader_1x10_P2.54mm_Vertical
J27: Conn_Scale3; PinHeader_1x10_P2.54mm_Vertical
J28: Conn_Relais; PinHeader_1x06_P2.54mm_Vertical
J29, J30, J32, J33, J34, J35: Conn_01x15_Male; PinHeader_1x15_P2.54mm_Vertical
J31: Conn_Scale4; PinHeader_1x10_P2.54mm_Vertical
PS1, PS2: LM2596
R1, R2, R3, R4, R5, R6: ERJ-6RBD1003V; R_0805_2012Metric_Pad1.15x1.40mm_HandSolder
TH1, TH2, TH3, TH4, TH5, TH6: Thermistor_NTC; PinHeader_1x02_P2.54mm_Vertical
XA1: Arduino_Mega2560_Shield
XA2, XA3, XA4: Arduino_Nano_Socket

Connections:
+5V: J4.1, J4.2, J4.3, J4.4, J4.5, J4.6, J4.7, J4.8, J8.2 (5V), J8.4 (5V), J9.1, J9.2, PS2.3 (OUT+)
+8V: J12.1, J30.1, J33.1, J35.1, PS1.3 (OUT+), XA1.VIN, XA2.VIN, XA3.VIN, XA4.VIN
+12V: J2.1 (PWR), PS1.2 (IN+), PS2.2 (IN+)
GND: C1.1, C2.1, C3.1, C4.1, C5.1, C6.1, C7.1, C8.1, C9.1, C10.1, C11.1, C12.1, C13.1, C14.1, C15.1, C16.1, C17.1, J1.1, J1.2, J1.3, J1.4, J1.5, J1.6, J1.7, J1.8, J2.2 (SENSE), J2.3 (GND), J5.1, J5.9, J5.13, J6.1, J6.9, J6.13, J7.1, J7.8, J7.16, J8.6 (GND), J8.9 (GND), J8.14 (GND), J8.20 (GND), J8.25 (GND), J8.30 (GND), J8.34 (GND), J8.39 (GND), J9.3, J9.7, J9.10, J9.15, J9.17, J10.3, J11.1, J12.2, J12.3, J15.5, J16.1, J17.2, J18.1, J18.2, J19.1, J20.4, J23.1, J24.1, J25.1, J26.1, J27.1, J28.1, J29.12, J30.2, J31.1, J32.12, J33.2, J34.12, J35.2, PS1.1 (IN-), PS1.4 (OUT-), PS2.1 (IN-), PS2.4 (OUT-), R1.1, R2.1, R3.1, R4.1, R5.1, R6.1, XA1.GND1 (GND), XA1.GND2 (GND), XA1.GND3 (GND), XA1.GND4 (SPI_GND), XA1.GND5 (GND), XA1.GND6 (GND), XA2.GND1 (GND), XA2.GND2 (GND), XA3.GND1 (GND), XA3.GND2 (GND), XA4.GND1 (GND), XA4.GND2 (GND)
MEGA_D20_SDA: J22.7, XA1.D20 (D20_SDA)
MEGA_D21_SCL: J22.8, XA1.D21 (D21_SCL)
MEGA_RX0: J21.8, XA1.D0 (D0_RX0)
MEGA_RX1: J11.3, J22.6, XA1.D19 (D19_RX1)
MEGA_RX2: J22.4, XA1.D17 (D17_RX2)
MEGA_RX3: J22.2, XA1.D15 (D15_RX3)
MEGA_RX4: J22.1, XA1.D14 (D14_TX3)
MEGA_TX0: J21.7, XA1.D1 (D1_TX0)
MEGA_TX1: J11.2, J22.5, XA1.D18 (D18_TX1)
MEGA_TX2: J22.3, XA1.D16 (D16_TX2)
M_3V3: C1.2, C3.2, C4.2, C5.2, C6.2, C7.2, C8.2, C9.2, C10.2, C13.2, J11.4, J12.5, J15.7, J16.3, J19.3, J23.10, J24.3, J25.3, J26.10, J27.10, J31.10, XA1.3V3 (3.3V)
M_5V: C2.2, C11.2, C12.2, C14.2, C15.2, C16.2, C17.2, J10.4, J12.4, J18.35, J18.36, TH1.1, TH2.1, TH3.1, TH4.1, TH5.1, TH6.1, XA1.5V1 (5V), XA1.5V3 (5V), XA1.5V4 (5V)
M_A0: J13.8, R1.2, TH1.2, XA1.A0
M_A1: J13.7, R2.2, TH2.2, XA1.A1
M_A2: J13.6, R3.2, TH3.2, XA1.A2
M_A3: J13.5, R4.2, TH4.2, XA1.A3
M_A4: J13.4, R5.2, TH5.2, XA1.A4
M_A5: J13.3, R6.2, TH6.2, XA1.A5
M_A6: J13.2, XA1.A6
M_A7: J13.1, XA1.A7
M_A8: J14.8, XA1.A8
M_A9: J14.7, XA1.A9
M_A10: J14.6, XA1.A10
M_A11: J14.5, XA1.A11
M_A12: J14.4, XA1.A12
M_A13: J14.3, XA1.A13
M_A14: J14.2, XA1.A14
M_A15: J14.1, XA1.A15
M_AREF: J20.3, XA1.AREF
M_D46: J18.9, XA1.D46
M_D47: J18.10, XA1.D47
M_D48: J18.7, XA1.D48
M_Flow1: J16.2, J20.8, XA1.D10
M_Flow2: J19.2, J20.7, XA1.D11
M_Flow3: J20.6, J24.2, XA1.D12
M_Flow4: J20.5, J25.2, XA1.D13
M_IORF: J12.7, XA1.IORF (IOREF)
M_MISO: J17.5, XA1.MISO (SPI_MISO)
M_MOSI: J17.4, XA1.MOSI (SPI_MOSI)
M_RST1: J12.6, XA1.RST1 (RESET)
M_RST2: J17.1, XA1.RST2 (SPI_RESET)
M_SCK: J17.3, XA1.SCK (SPI_SCK)
M_SPI_5V: J17.6, XA1.5V2 (SPI_5V)
N1_3V3: J30.14, XA2.3V3 (3.3V)
N1_5V: J28.6, J30.4, XA2.5V
N1_A0: J30.12, XA2.A0
N1_A1: J30.11, XA2.A1
N1_A2: J30.10, XA2.A2
N1_A3: J30.9, XA2.A3
N1_A6: J30.6, XA2.A6
N1_A7: J30.5, XA2.A7
N1_AREF: J30.13, XA2.AREF
N1_D0: J29.14, XA2.D0 (D0_RX0)
N1_D1: J29.15, XA2.D1 (D1_TX0)
N1_D2_INT0: J29.11, XA2.D2 (D2_INT0)
N1_D3_INT1: J29.10, XA2.D3 (D3_INT1)
N1_D4: J29.9, XA2.D4
N1_D5: J29.8, XA2.D5
N1_D6: J29.7, XA2.D6
N1_D7: J29.6, XA2.D7
N1_D8: J29.5, XA2.D8
N1_D9: J29.4, XA2.D9
N1_RST1: J29.13, XA2.RST1 (RESET)
N1_RST2: J30.3, XA2.RST2 (RESET)
N2_3V3: J33.14, XA3.3V3 (3.3V)
N2_5V: J33.4, XA3.5V
N2_A0: J33.12, XA3.A0
N2_A1: J33.11, XA3.A1
N2_A2: J33.10, XA3.A2
N2_A3: J33.9, XA3.A3
N2_A6: J33.6, XA3.A6
N2_A7: J33.5, XA3.A7
N2_AREF: J33.13, XA3.AREF
N2_D0: J32.14, XA3.D0 (D0_RX0)
N2_D1: J32.15, XA3.D1 (D1_TX0)
N2_D2_INT0: J32.11, XA3.D2 (D2_INT0)
N2_D3_INT1: J32.10, XA3.D3 (D3_INT1)
N2_D4: J32.9, XA3.D4
N2_D5: J32.8, XA3.D5
N2_D6: J32.7, XA3.D6
N2_D7: J32.6, XA3.D7
N2_D8: J32.5, XA3.D8
N2_D9: J32.4, XA3.D9
N2_D10: J32.3, XA3.D10 (D10_CS)
N2_D11: J32.2, XA3.D11 (D11_MOSI)
N2_D12: J32.1, XA3.D12 (D12_MISO)
N2_D13: J33.15, XA3.D13 (D13_SCK)
N2_RST1: J32.13, XA3.RST1 (RESET)
N2_RST2: J33.3, XA3.RST2 (RESET)
N3_3V3: J35.14, XA4.3V3 (3.3V)
N3_5V: J35.4, XA4.5V
N3_A0: J35.12, XA4.A0
N3_A1: J35.11, XA4.A1
N3_A2: J35.10, XA4.A2
N3_A3: J35.9, XA4.A3
N3_A6: J35.6, XA4.A6
N3_A7: J35.5, XA4.A7
N3_AREF: J35.13, XA4.AREF
N3_D0: J34.14, XA4.D0 (D0_RX0)
N3_D1: J34.15, XA4.D1 (D1_TX0)
N3_D2_INT0: J34.11, XA4.D2 (D2_INT0)
N3_D3_INT1: J34.10, XA4.D3 (D3_INT1)
N3_D4: J34.9, XA4.D4
N3_D5: J34.8, XA4.D5
N3_D6: J34.7, XA4.D6
N3_D7: J34.6, XA4.D7
N3_D8: J34.5, XA4.D8
N3_D9: J34.4, XA4.D9
N3_D10: J34.3, XA4.D10 (D10_CS)
N3_D11: J34.2, XA4.D11 (D11_MOSI)
N3_D12: J34.1, XA4.D12 (D12_MISO)
N3_D13: J35.15, XA4.D13 (D13_SCK)
N3_RST1: J34.13, XA4.RST1 (RESET)
N3_RST2: J35.3, XA4.RST2 (RESET)
NFC_MISO: J15.4, J18.5, XA1.D50
NFC_MOSI: J15.3, J18.6, XA1.D51
NFC_RST: J15.6, J18.8, XA1.D49
NFC_SCK: J15.2, J18.3, XA1.D52
NFC_SDA: J15.1, J18.4, XA1.D53 (D53_SS)
RPI_GPIO4: J5.3, J6.3, J7.17, J8.7 (GCLK0/GPIO4)
RPI_GPIO5: J6.15, J7.6, J8.29 (GCLK1/GPIO5)
RPI_GPIO6: J6.14, J7.5, J8.31 (GCLK2/GPIO6)
RPI_GPIO7: J5.14, J8.26 (~CE1~/GPIO7), J9.13
RPI_GPIO8: J5.12, J8.24 (~CE0~/GPIO8), J9.12
RPI_GPIO9: J5.11, J7.10, J8.21 (MISO0/GPIO9)
RPI_GPIO10: J5.10, J7.11, J8.19 (MOSI0/GPIO10)
RPI_GPIO11: J5.16, J7.9, J8.23 (SCLK0/GPIO11)
RPI_GPIO12: J6.16, J8.32 (PWM0/GPIO12), J9.16
RPI_GPIO13: J6.11, J7.4, J8.33 (PWM1/GPIO13)
RPI_GPIO14: J8.8 (GPIO14/TXD), J9.4
RPI_GPIO15: J8.10 (GPIO15/RXD), J9.5
RPI_GPIO16: J8.36 (GPIO16), J9.18
RPI_GPIO17: J5.4, J6.4, J7.15, J8.11 (GPIO17)
RPI_GPIO18: J5.2, J6.2, J8.12 (GPIO18/PWM0), J9.6
RPI_GPIO19: J6.12, J7.3, J8.35 (GPIO19/MISO1)
RPI_GPIO20: J6.10, J8.38 (GPIO20/MOSI1), J9.19
RPI_GPIO21: J8.40 (GPIO21/SCLK1), J9.20
RPI_GPIO22: J5.8, J6.8, J7.13, J8.15 (GPIO22)
RPI_GPIO23: J5.7, J6.7, J8.16 (GPIO23), J9.8
RPI_GPIO24: J5.6, J6.6, J8.18 (GPIO24), J9.9
RPI_GPIO25: J5.5, J6.5, J8.22 (GPIO25), J9.11
RPI_GPIO26: J7.2, J8.37 (GPIO26)
RPI_GPIO27: J5.15, J7.14, J8.13 (GPIO27)
RPI_IDSC: J8.28 (ID_SC/GPIO1), J9.14
RPI_IDSD: J7.7, J8.27 (ID_SD/GPIO0)
Relais1: J28.5, J30.15, XA2.D13 (D13_SCK)
Relais2: J28.4, J29.1, XA2.D12 (D12_MISO)
Relais3: J28.3, J29.2, XA2.D11 (D11_MOSI)
Relais4: J28.2, J29.3, XA2.D10 (D10_CS)
SCL: J7.18, J8.5 (SCL/GPIO3), J10.1, J20.1, J30.7, J33.7, J35.7, XA1.SCL, XA2.A5 (A5_SCL), XA3.A5 (A5_SCL), XA4.A5 (A5_SCL)
SDA: J7.19, J8.3 (SDA/GPIO2), J10.2, J20.2, J30.8, J33.8, J35.8, XA1.SDA, XA2.A4 (A4_SDA), XA3.A4 (A4_SDA), XA4.A4 (A4_SDA)
Sc1_DT1: J18.27, J23.3, XA1.D28
Sc1_DT2: J18.29, J23.5, XA1.D26
Sc1_DT3: J18.31, J23.7, XA1.D24
Sc1_DT4: J18.33, J23.9, XA1.D22
Sc1_SCK1: J18.28, J23.2, XA1.D29
Sc1_SCK2: J18.30, J23.4, XA1.D27
Sc1_SCK3: J18.32, J23.6, XA1.D25
Sc1_SCK4: J18.34, J23.8, XA1.D23
Sc2_DT1: J18.19, J26.3, XA1.D36
Sc2_DT2: J18.21, J26.5, XA1.D34
Sc2_DT3: J18.23, J26.7, XA1.D32
Sc2_DT4: J18.25, J26.9, XA1.D30
Sc2_SCK1: J18.20, J26.2, XA1.D37
Sc2_SCK2: J18.22, J26.4, XA1.D35
Sc2_SCK3: J18.24, J26.6, XA1.D33
Sc2_SCK4: J18.26, J26.8, XA1.D31
Sc3_DT1: J18.11, J27.3, XA1.D44
Sc3_DT2: J18.13, J27.5, XA1.D42
Sc3_DT3: J18.15, J27.7, XA1.D40
Sc3_DT4: J18.17, J27.9, XA1.D38
Sc3_SCK1: J18.12, J27.2, XA1.D45
Sc3_SCK2: J18.14, J27.4, XA1.D43
Sc3_SCK3: J18.16, J27.6, XA1.D41
Sc3_SCK4: J18.18, J27.8, XA1.D39
Sc4_DT1: J20.10, J31.3, XA1.D8
Sc4_DT2: J21.2, J31.5, XA1.D6
Sc4_DT3: J21.4, J31.7, XA1.D4
Sc4_DT4: J21.6, J31.9, XA1.D2 (D2_INT0)
Sc4_SCK1: J20.9, J31.2, XA1.D9
Sc4_SCK2: J21.1, J31.4, XA1.D7
Sc4_SCK3: J21.3, J31.6, XA1.D5
Sc4_SCK4: J21.5, J31.8, XA1.D3 (D3_INT1)

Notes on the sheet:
LED Matrix Connection
Scale1
Scale2
Fingerprint
Flowmeter
RPi Breakout
NFC
Relais-Connection
Mega Breakout
Nano #1 Breakout
Nano #2 Breakout
Nano #3 Breakout
Power Input
I2C 7 Segment Display
Scale3
Scale4
Temp1
Temp2
Temp4
Temp3
Temp5
Temp6

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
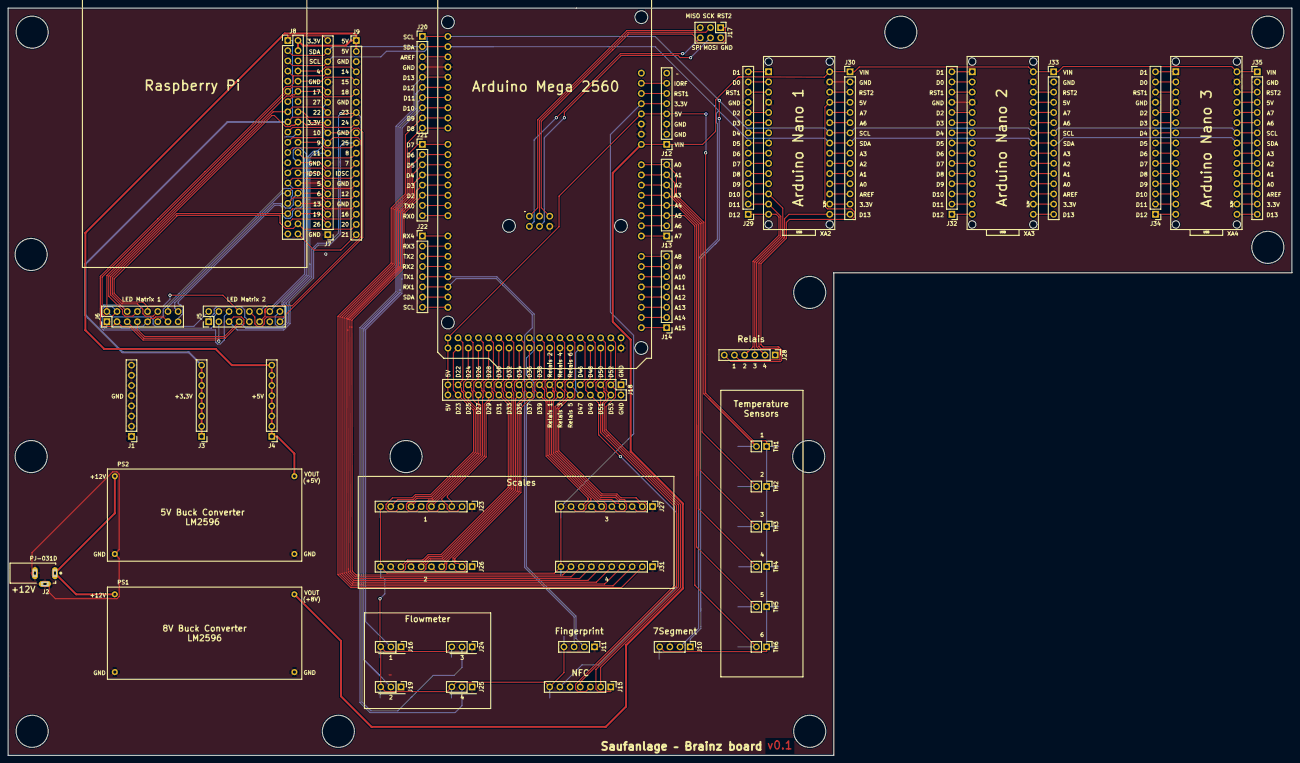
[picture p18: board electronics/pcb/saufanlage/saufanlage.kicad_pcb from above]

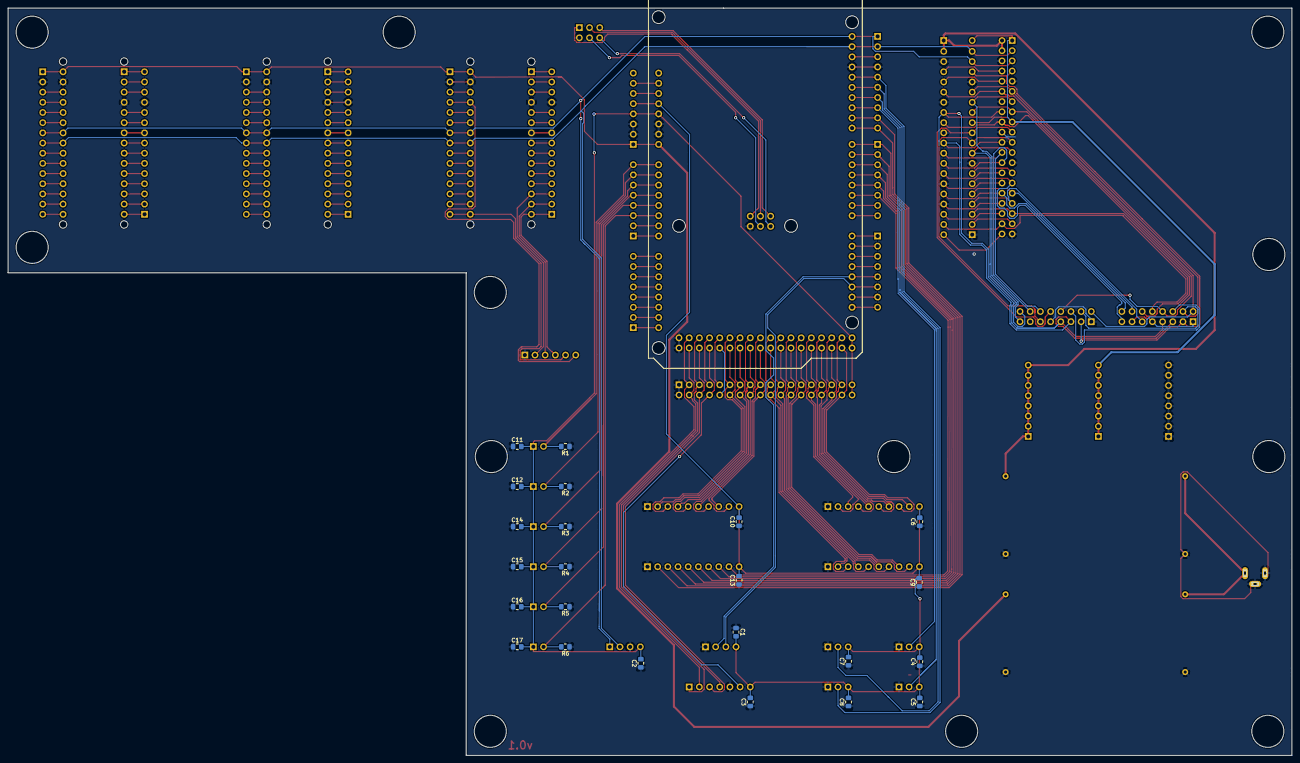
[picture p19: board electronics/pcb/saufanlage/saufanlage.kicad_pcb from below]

Board: 2 copper layers, 320.3 x 186.4 mm, 70 parts (24 on the bottom side), 188 nets.

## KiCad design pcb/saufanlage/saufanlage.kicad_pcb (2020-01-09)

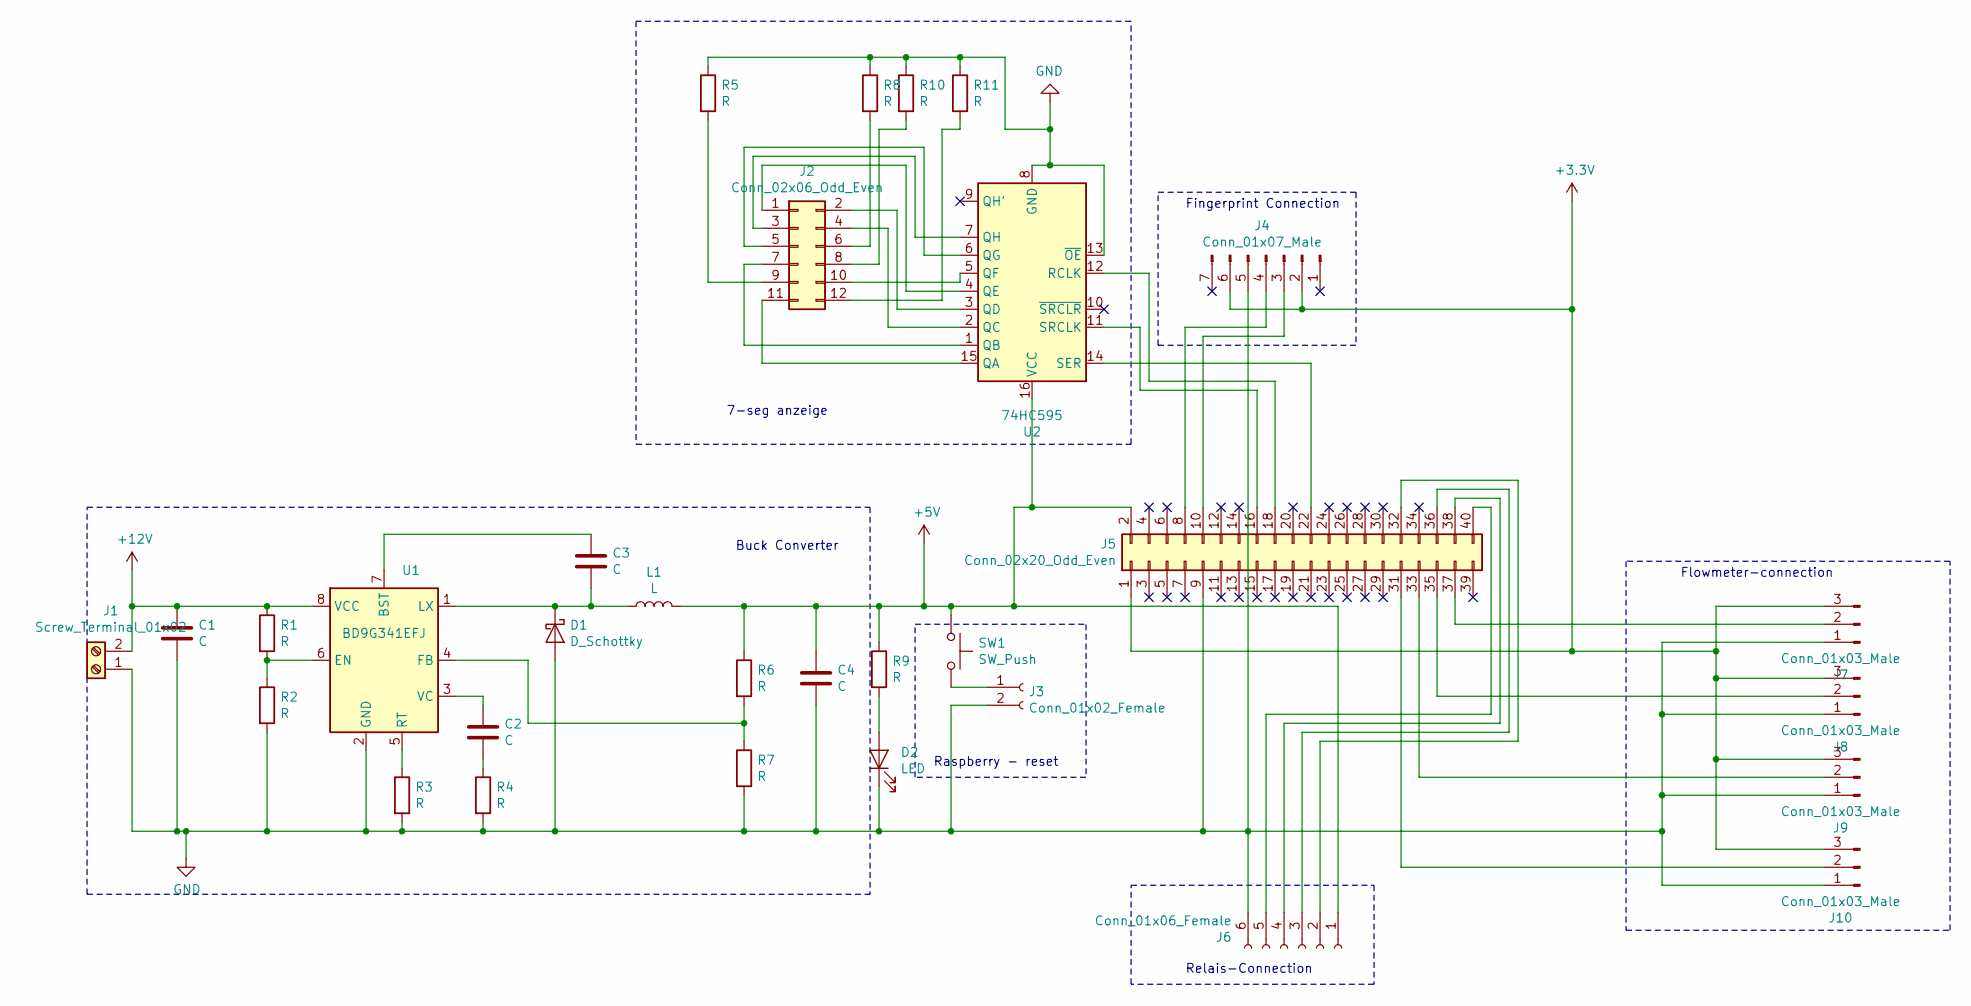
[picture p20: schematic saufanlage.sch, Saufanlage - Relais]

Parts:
C1: C; C_2220_5650Metric_Pad1.97x5.40mm_HandSolder
C2: C; C_1206_3216Metric_Pad1.42x1.75mm_HandSolder
C3: C; C_0805_2012Metric_Pad1.15x1.40mm_HandSolder
C4: C; C_1812_4532Metric_Pad1.30x3.40mm_HandSolder
D1: D_Schottky; D_SOT-23_ANK
D2: LED; LED_0805_2012Metric_Pad1.15x1.40mm_HandSolder
J1: Screw_Terminal_01x02; TerminalBlock_Altech_AK300-2_P5.00mm
J2: Conn_02x06_Odd_Even; IDC-Header_2x06_P2.54mm_Vertical
J3: Conn_01x02_Female; PinSocket_1x02_P2.54mm_Vertical
J4: Conn_01x07_Male; JST_EH_B7B-EH-A_1x07_P2.50mm_Vertical
J5: Conn_02x20_Odd_Even; PinSocket_2x20_P2.54mm_Vertical
J6: Conn_01x06_Female; PinSocket_1x06_P2.54mm_Vertical
J7, J8, J9, J10: Conn_01x03_Male; FanPinHeader_1x03_P2.54mm_Vertical
L1: L; L_12x12mm_H8mm
R1, R2, R3, R4, R5, R6, R7, R8, R9, R10, R11: R; R_0805_2012Metric_Pad1.15x1.40mm_HandSolder
SW1: SW_Push; SW_SPST_CK_RS282G05A3
U1: BD9G341EFJ; HTSOP-8-1EP_3.9x4.9mm_P1.27mm_EP2.4x3.2mm_ThermalVias
U2: 74HC595; DIP-16_W7.62mm_Socket

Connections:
+3V3: J4.2, J4.6, J5.1, J7.3, J8.3, J9.3, J10.3
+5V: C4.1, J5.2, J6.1, L1.2, R6.1, R9.1, SW1.1, U2.16 (VCC)
+12V: C1.1, J1.2, R1.1, U1.8 (VCC)
GND: C1.2, C4.2, D1.2 (A), D2.1 (K), J1.1, J3.2, J4.5, J5.9, J6.6, J7.1, J8.1, J9.1, J10.1, R2.2, R3.2, R4.2, R5.1, R7.2, R8.1, R10.1, R11.1, U1.2 (GND), U2.8 (GND), U2.13 (~OE)
unnamed: C2.1, U1.3 (VC)
unnamed: C2.2, R4.1
unnamed: C3.1, U1.7 (BST)
unnamed: C3.2, D1.1 (K), L1.1, U1.1 (LX)
unnamed: D2.2 (A), R9.2
unnamed: J2.1, U2.4 (QE)
unnamed: J2.2, U2.3 (QD)
unnamed: J2.3, U2.7 (QH)
unnamed: J2.4, U2.2 (QC)
unnamed: J2.5, U2.6 (QG)
unnamed: J2.6, R8.2
unnamed: J2.7, U2.1 (QB)
unnamed: J2.8, R10.2
unnamed: J2.9, R5.2
unnamed: J2.10, U2.5 (QF)
unnamed: J2.11, U2.15 (QA)
unnamed: J2.12, R11.2
unnamed: J3.1, SW1.2
unnamed: J4.3, J5.10
unnamed: J4.4, J5.8
unnamed: J5.16, U2.11 (SRCLK)
unnamed: J5.18, U2.12 (RCLK)
unnamed: J5.22, U2.14 (SER)
unnamed: J5.32, J6.2
unnamed: J5.33, J9.2
unnamed: J5.35, J8.2
unnamed: J5.36, J6.3
unnamed: J5.37, J7.2
unnamed: J5.38, J6.4
unnamed: J5.40, J6.5
unnamed: J5.31, J10.2
unnamed: R1.2, R2.1, U1.6 (EN)
unnamed: R3.1, U1.5 (RT)
unnamed: R6.2, R7.1, U1.4 (FB)

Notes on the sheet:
Buck Converter
Flowmeter-connection
Relais-Connection
Raspberry - reset
Fingerprint Connection
7-seg anzeige

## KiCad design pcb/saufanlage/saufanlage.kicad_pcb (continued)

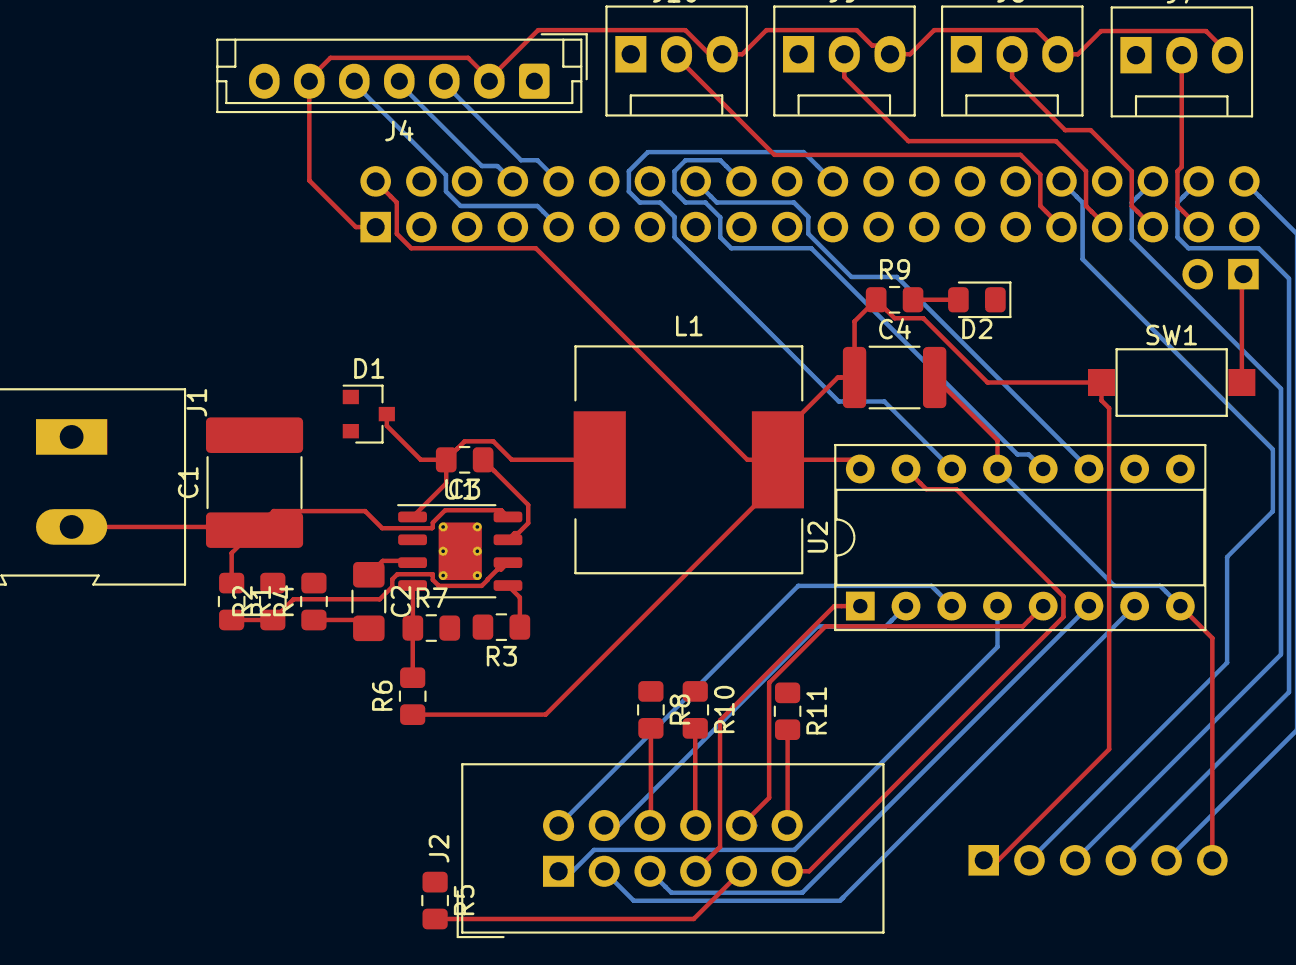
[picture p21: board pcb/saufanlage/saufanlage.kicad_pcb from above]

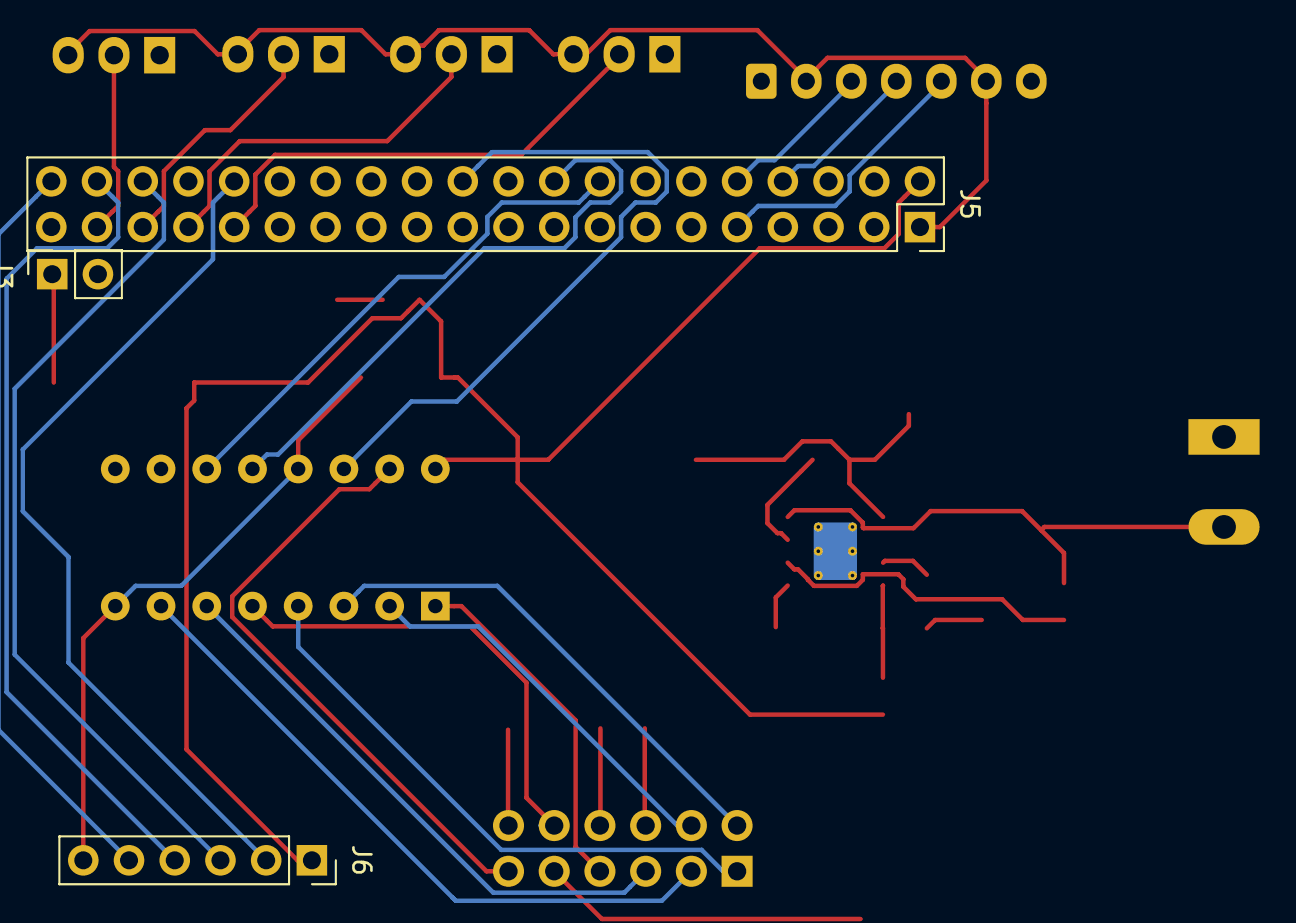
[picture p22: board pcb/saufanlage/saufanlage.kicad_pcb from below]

Board: 2 copper layers, 31 parts (3 on the bottom side), 38 nets.

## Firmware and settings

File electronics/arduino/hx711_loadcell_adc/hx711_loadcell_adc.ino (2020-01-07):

/*
 * (c) 2020 Andreas Hoenle
 *
 * Driver for the HX711 load cells interfacing an Arduino (mega)
 */

// https://github.com/olkal/HX711_ADC
#include <HX711_ADC.h>

HX711_ADC LoadCell(4, 5); // dt pin, sck pin

void setup()
{
    LoadCell.begin();             // start connection to HX711
    LoadCell.start(2000);         // load cells gets 2000ms of time to stabilize
    LoadCell.setCalFactor(999.0); // calibration factor for load cell => strongly dependent on your individual setup
    Serial.begin(9600);
    Serial.println("Setup complete.");
}

void loop()
{
    LoadCell.update();            // retrieves data from the load cell
    float i = LoadCell.getData(); // get output value
    Serial.println(i);
}

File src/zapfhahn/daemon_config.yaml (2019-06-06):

flowmeters:
- name: flowmeter_slot0
  pin: 26
  slot: 0
- name: flowmeter_slot1
  pin: 19
  slot: 1
- name: flowmeter_slot2
  pin: 13
  slot: 2
- name: flowmeter_augustiner_hell
  pin: 5
  slot: 3
valve_global_timeout_seconds: 40
valves:
- name: valve_slot0
  pin: 21
  quantity_ml: 500
  slot: 0
  timeout_seconds: 20
- name: valve_slot1
  pin: 20
  quantity_ml: 500
  slot: 1
  timeout_seconds: 20
- name: valve_slot2
  pin: 16
  quantity_ml: 500
  slot: 2
  timeout_seconds: 20
- name: valve_augustiner_hell
  pin: 12
  quantity_ml: 700
  slot: 3
  timeout_seconds: 90

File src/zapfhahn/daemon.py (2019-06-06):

"""
(c) 2019 Andreas Hoenle (andreas.hoenle@gmail.com)

The continuously running daemon that gives us beer
"""

import os

import RPi.GPIO as GPIO
import time
import yaml

from statemachine import StateMachine, State

from utils.log import get_logger

from database.dblog import DbLogger
from hardware.fourdigitdisplay import display
from database.usermanager import FingerprintFinder
from hardware.fingerprint import SaufFinger
from hardware.flowmeter import Flowmeter
from hardware.valve import MagneticValve

from logging import DEBUG

log = get_logger(os.path.basename(__file__), level=DEBUG)

config_file = "daemon_config.yaml"


class StateAttributes:
    """
    helper class that stores all the changing attributes that are required in the
    various states
    """

    # user_index of the database entry that is being processes
    user_index = None
    # name of the person behind the user_index
    user_name = ""
    # fingerprint info
    fingerprint = None
    # valve info
    valve_slot = -1
    valve_pin = -1
    valve_name = ""
    valve_quantity_ml = -1
    valve_timeout_seconds = -1
    valve_open_time = ""
    valve_close_time = ""
    # counter info
    counter_name = ""
    counter_pin = -1
    counter_slot = -1
    counter_ticks = -1
    counter_global_ticks = -1
    counter_conv_factor = -1
    quantity_ml = 0
    # tapping procedure exit status
    tap_status = "STATUS_UNKNW"
    # screenshot names from webcam
    screenshot1 = ""
    screenshot2 = ""
    # misc
    misc = ""

    def add_valve(self, valve):
        if not valve:
            return
        self.valve_pin = valve.pin
        self.valve_slot = valve.slot
        self.valve_name = valve.name
        self.valve_quantity_ml = valve.quantity_ml
        self.valve_timeout_seconds = valve.timeout_seconds

    def add_counter(self, counter):
        if not counter:
            return
        self.counter_name = counter.name
        self.counter_pin = counter.pin
        self.counter_slot = counter.slot
        self.counter_ticks = counter.ticks
        self.counter_global_ticks = counter.global_count["ticks"]
        self.counter_conv_factor = counter.conversion_factor
        self.quantity_ml = counter.ml


class SaufDaemon(StateMachine):
    """
    A class of settings that implements a run function that implements the daemon.
    The daemon is implemented as a state machine
    """

    # reset state
    reset = State("reset", initial=True)
    # waiting for fingerprint sensor input
    waiting_finger = State("waiting_finger")
    # checking the ID
    checking = State("checking")
    # opening the valves
    opening = State("opening")
    # waiting for valves to measure requested quantity
    waiting_valve = State("waiting_valve")
    # closing the valves
    closing = State("closing")
    # logging the tapped quantity
    logging = State("logging")
    error = State("error")

    next = reset.to(waiting_finger)
    next |= waiting_finger.to(checking)
    next |= checking.to(opening)
    next |= opening.to(waiting_valve)
    next |= waiting_valve.to(closing)
    next |= closing.to(logging)
    next |= logging.to(waiting_finger)

    def __init__(self, name):
        self.name = name
        # global configuration
        self.config = self.load_config()
        # attributes that need to be carried from one state to another
        self.attributes = StateAttributes()
        # hardware
        self.finger = SaufFinger()
        self.finder = FingerprintFinder()
        self.valves = self.__init_valves()
        self.flowmeters = self.__init_flowmeters()
        self.__sanity_checks()
        # database
        self.dblog = DbLogger()

    def __del__(self):
        """ cleanup GPIO """
        GPIO.cleanup()

    def _dump_config(self):
        """ expert use only! dump and overwrite current config on disk """
        with open(config_file, "w") as cfg_out:
            yaml.dump(self.config, cfg_out, default_flow_style=False)

    def __init_valves(self):
        """ initialize the valves with settings from the global config """
        log.info("Initializing %d valves", len(self.config["valves"]))
        return [MagneticValve(**settings) for settings in self.config["valves"]]

    def __init_flowmeters(self):
        """ initialize the flowmeters with settings from the global config """
        log.info("Initializing %d flowmeters", len(self.config["flowmeters"]))
        return [Flowmeter(**settings) for settings in self.config["flowmeters"]]

    def __sanity_checks(self):
        """ run sanity checks to avoid undefined behaviour later """
        for valve in self.valves:
            for meter in self.flowmeters:
                if meter.slot == valve.slot:
                    break
            else:
                raise RuntimeError(
                    "Registered valve in slot {} has now corresponding flowmeter".format(
                        valve.slot
                    )
                )
        for meter in self.flowmeters:
            for valve in self.valves:
                if valve.slot == meter.slot:
                    break
            else:
                raise RuntimeError(
                    "Registered flowmeter in slot {} has now corresponding valve".format(
                        valve.slot
                    )
                )

    def load_config(self):
        """ load settings from a yaml file on disk """
        if os.path.isfile(config_file):
            with open(config_file) as cfg_in:
                return yaml.load(cfg_in)
        # no config file - default settings
        return {
            "valve_global_timeout_seconds": 40,
            "valves": [
                {
                    "name": "valve_slot0",
                    "pin": 21,
                    "slot": 0,
                    "quantity_ml": 500,
                    "timeout_seconds": 20,
                },
                {
                    "name": "valve_slot1",
                    "pin": 20,
                    "slot": 1,
                    "quantity_ml": 500,
                    "timeout_seconds": 20,
                },
                {
                    "name": "valve_slot2",
                    "pin": 16,
                    "slot": 3,
                    "quantity_ml": 500,
                    "timeout_seconds": 20,
                },
                {
                    "name": "valve_slot3",
                    "pin": 12,
                    "slot": 4,
                    "quantity_ml": 500,
                    "timeout_seconds": 20,
                },
            ],
            "flowmeters": [
                {"name": "flowmeter_slot0", "pin": 26, "slot": 0},
                {"name": "flowmeter_slot1", "pin": 19, "slot": 1},
                {"name": "flowmeter_slot2", "pin": 13, "slot": 3},
                {"name": "flowmeter_slot3", "pin": 6, "slot": 4},
            ],
        }
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

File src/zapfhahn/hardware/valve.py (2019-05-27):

"""
(c) 2019 Andreas Hoenle (andreas.hoenle@gmail.com)

Wrapper around the valves
"""

import RPi.GPIO as GPIO

GPIO.setmode(GPIO.BCM)

class MagneticValve():
    """ normally closed magnetic valve """
    def __init__(self, **kwargs):
        """
        Default initialiser

        Args:
            name: A name to identify the valve
            pin: The Raspberry Pi GPIO Pin
            slot: The slot in the setup (we usually count the taps from 0..3)
            quantity_ml: Allowed quantity to be tapped before auto-close
            timeout_seconds: Allowed time before auto-close

        Important: Auto-closing needs to be implemented elsewhere.
        Note: Currently we do the auto-closing in the daemon.
        """
        required_kwargs = ["name", "pin", "slot", "quantity_ml", "timeout_seconds"]
        for req in required_kwargs:
            if req not in kwargs:
                raise AttributeError("Missing required argument for MagenticValve: {}".format(req))
        for key, val in kwargs.items():
            setattr(self, key, val)
        GPIO.setup(self.pin, GPIO.OUT)
        self.close()

    def open(self):
        """ open the valve by setting the pin to LOW """
        GPIO.output(self.pin, GPIO.LOW)

    def close(self):
        """ close the valve by setting the pin to HIGH """
        GPIO.output(self.pin, GPIO.HIGH)

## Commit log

2019-02-23 Add switcher flask app with dummy slide button
2019-02-24 Rename switcherapp -> app
2019-02-24 Save switch states to disk
2019-03-09 Add RGB Matrix driver as submodule
2019-04-01 Add flowmeter
2019-04-28 Add wiring to README
2019-04-29 Modified readme to complete the UART config.
2019-05-27 Add daemon
    [flowmeter_calib.yml]
2019-05-31 It's alive!
    [flowmeter_calib.yml]
2019-06-02 Last octopi commit :spaceship:
    [flowmeter_calib.yml]
2019-06-02 Update switchstates
2019-06-04 Cleanup repo :paperclip:
    [flowmeter_calib.yml]
2019-06-04 Start playing with User and Fingerprint classes
2019-06-12 Added first draft of Circuit Board
    [saufanlage.kicad_pcb, saufanlage.sch]
2019-12-03 Add some stuff for electronics
    [saufanlage.kicad_pcb, saufanlage.sch]
2020-01-07 Update electronics stuff
    [PCB2020.sch, load_cells_connector_board.kicad_pcb, load_cells_connector_board.sch]
2020-01-08 Saufanlagen PCB update
    [saufanlage-Zero-header.kicad_pcb, saufanlage.kicad_pcb, saufanlage.sch]
2020-01-09 Add connectors
2020-01-12 Backup commit
    [Arduino-Uno-r3-with-RFID-RC522.fzz, saufanlage.kicad_pcb, saufanlage.sch]
2020-01-12 Label Flowmeter
    [saufanlage.kicad_pcb]
2020-01-14 More brainz updates
    [PCB2020.sch, saufanlage-Zero-header.kicad_pcb, saufanlage.kicad_pcb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]
2020-02-10 Add fourth scale and temp sensor
    [saufanlage.sch]
2020-02-10 Add I2C 7 Segment test
2020-03-18 Add temperature sensors
    [saufanlage.kicad_pcb, saufanlage.sch]
2020-03-19 Clean up tracks
    [saufanlage.kicad_pcb]
2020-03-19 Add caps
    [saufanlage.kicad_pcb, saufanlage.sch]
